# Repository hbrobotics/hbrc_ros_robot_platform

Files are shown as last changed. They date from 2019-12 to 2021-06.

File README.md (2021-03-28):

<!--
MIT License

Copyright 2020 Home Brew Robotics Club

Permission is hereby granted, free of charge, to any person obtaining a copy of this
software and associated documentation files (the "Software"), to deal in the Software
without restriction, including without limitation the rights to use, copy, modify,
merge, publish, distribute, sublicense, and/or sell copies of the Software, and to
permit persons to whom the Software is furnished to do so, subject to the following
conditions:

The above copyright notice and this permission notice shall be included in all copies
or substantial portions of the Software.

THE SOFTWARE IS PROVIDED "AS IS", WITHOUT WARRANTY OF ANY KIND, EXPRESS OR IMPLIED,
INCLUDING BUT NOT LIMITED TO THE WARRANTIES OF MERCHANTABILITY, FITNESS FOR A PARTICULAR
PURPOSE AND NONINFRINGEMENT. IN NO EVENT SHALL THE AUTHORS OR COPYRIGHT HOLDERS BE LIABLE
FOR ANY CLAIM, DAMAGES OR OTHER LIABILITY, WHETHER IN AN ACTION OF CONTRACT, TORT OR
OTHERWISE, ARISING FROM, OUT OF OR IN CONNECTION WITH THE SOFTWARE OR THE USE OR OTHER
DEALINGS IN THE SOFTWARE.
-->

# HBRC ROS Robot Platform

The HBRC ROS Robot platform (ie. HR<Sup>2</Sup> or just plain HR2) is a
pedagogical robotic platform for teaching various robotics skills.

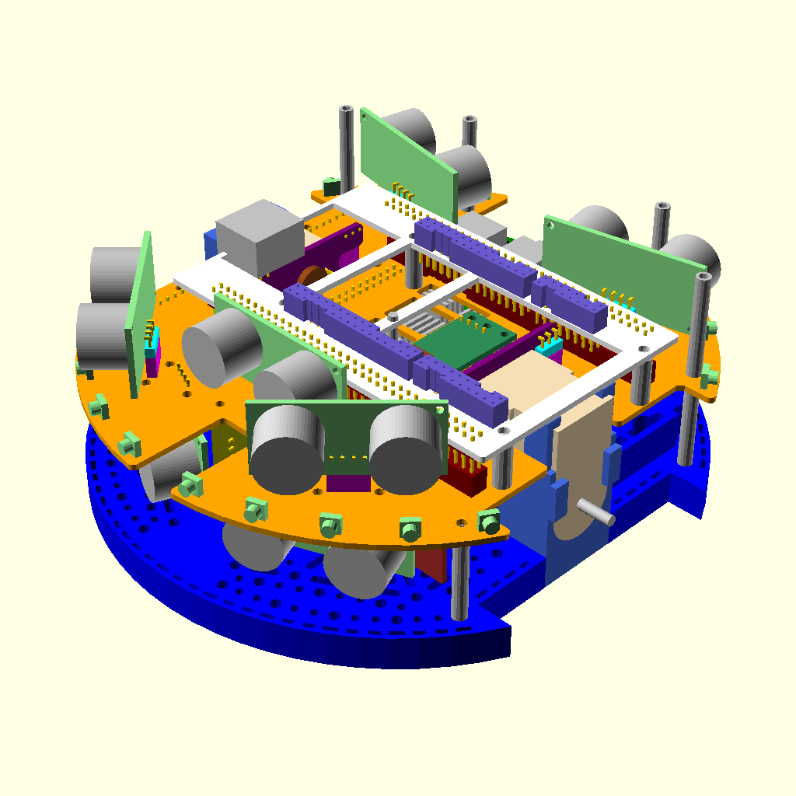
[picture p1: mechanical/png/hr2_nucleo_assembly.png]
HR2 Robot


This top level document is broken into the following sections below:

* [Google Group](#google-group):
  The Google Group mailing list for this project.

* [Goals/Requirements](#goalsrequirements):
  The goals and requirements for the project.

* [Mechanical](#mechanical):
  The mechanical engineering aspects of the project.

* [Electrical](#electrical):
  The electrical engineering aspects of the project.

* [Software](#software):
  The software engineering aspects of the project.

* [Education](#education):
  The education components of the project.

* [Download, Installation and Workflow](#download-installation-and-workflow):
  The download, installation, and workflow portions of the project.

* [Talks](#talks):
  Various talks given about the project.

## Google Group

There is a Google Groups mailing list to discuss this project at
[HbrcRosRobotPlatform@GoogleGroups.Com](mailto:HbrcRosRobotPlatform@GoogleGroups.Com).
To join the group, visit the
[HBRC ROS Robot Platform web page](https://groups.google.com/d/forum/hbrcrosrobotplatform)
(i.e. `https://groups.google.com/d/forum/hbrcrosrobotplatform`) and request to join.
If that does not work, squirt a quick message to the group manager
(`Wayne` AT_SIGN `Gramlich` PERIOD `Net`) requesting an invitation to join the group.

Not all traffic on the group is going to be interesting to everybody else.
To help out with filtering please put one of the following prefixes at the
front of the each subject line:

* `ALL:` A message of interest to everybody.
* `INST:` A message concerning software installation.
* `ME:` A message to people interested in the HR2 Mechanical Engineering 
  (i.e. solid modeling.)
* `EE:` A message to people interested in the HR2 Electrical Engineering
  (i.e. PCB design, manufacture, bring-up, testing, etc.)
* `SE:` A message to people interested in the HR2 Software Engineering
  (i.e. programs, firmware, etc.)
* `ED:` A message to people interested in the HR2 course materials.
* `DEV:` A message concerning downloading, installation, and development.
* `MSC:` A miscellaneous message that does not really fit any of the above
  protocols.

That should be enough group mailing list structure for starters.

## Goals/Requirements

The list below summarizes the some of the design choices that have been
made so far.

* Start with the Pololu Romi platform used by FPGA class. [Decided]
* Use Patrick's PCB breakout board as a starting point. [Done]
* Consider ditching the Pololu motor board. [Done]
* Work hard to see if the Pololu arm can be bolted on. [Very Likely]
* Try to use USB battery pack instead of AA batteries. [USB Pack yes; AA's no]
* Provide support RasPi 3B+ and RasP4: [yes]
  * 40-pin connector.
  * I2C EEPROM for "hat" identification.
  * Real Time Clock needed for ROS.
  * Various RasPi I2C, SPI, GPO, Serial lines made available.
    *  [Serial: yes, I2C: yes, SPI: probably not, GPIO: OS shutdown
* Some sort of MPU on board:
  * Off the shelf microcontroller board [STM Nucleo-144 Dev. Board format selected]
  * Roomy enough to run MicroPython/MicroROS [STM NUCLEO-F767ZI nominal]
    * ~$25, 216MHz, 2MB Flash, 512K RAM, timers, UARTs, I2C, SPI, Ethernet, etc.
  * Must support C/C++ debugging [ST-Link].
  * Ethernet Phy to talk to boards other than RasPi [Yes]
* FPGA support [custom daughter board required.]
* Arduino support [AVR Dropped. AVR's are expensive/under powered]
* Expansion Capabilities:
  * Arduino Shields. [One can be plugged onto Nucleo.]
  * MikroBus [Iffy, space is tight]
  * Demand Peripherals Connector(s): [On FPGA daughter boards only]
  * Wayne's Bus? [Iffy, space is tight; ouch this hurts!]
  * Grove connectors [Very Likely]
  * Pololu power supply sockets [Iffy, space is tight.]
* Sensors:
  * Motor encoders. [Yes, 1440 step/rev.]
  * Various edge sensors for table top challenge, maze follower, etc.
  * Edge sensors (TOF, IR)
  * Sonars, the are cheap [5 in front, 4 in back.]
  * Servos (arm, camera tilt) [Minimum 4 required]
  * Inexpensive Lidar [Only if the platform is not overloaded]
    * YLidar X2 (~$70)
    * RPLdar A1M8 (~$100)
  * E-Stop [Probably not]
* Camera [RasPi Camera]
* Misc:
  * What issues are missing?

### Mechanical

The mechanical issues are worked out in greater detail in the
[mechancial directory](mechanical/README.md).

The mechanical tasks are:

* Model the Romi platform in OpenSCAD to ensure that the PCB outline
  and mounting holes are correct.
* Model the Romi arm in OpenSCAD to make sure that the Arm does not
  interfere with anything.
* Model both a RasPi 3B+ and RasPi4 for attaching to PCB.
* Model the basic PCB outlines, connector placements, etc.

A short summary of the mechanical design decisions to date are:

* Use the Pololu Romi Platform.
* Use an alternate layout of the motor encoder PCB to free up space to
  support some SBC (Single Board Computers) that are larger than the
  Raspberry Pi footprint.
* Design master board to use an STM Nucleo-144 development board for the
  processor.  All H-bridges, power management, to be put on one board.
* FPGA boards to be done with a a daughter board that plugs into Nucleo-144 board.
 
## Electrical

The electrical issues are worked out in greater detail in the
[electrical directory](electrical/README.md).

Some brief comments on the electrical aspects are:

* The design is to be done using KiCad, since KiCad is 100% free.
* It would be nice to be able to use a simple two layer PCB.
* It would be nice to be able to take power from a USB Power pack.
* It would be nice to support daughter boards for FPGA's.

The overall strategy is to prototype everything using the
[Bantum Labs PCB Milling Machine](https://www.bantamtools.com/)
over at [OLogic](http://www.ologicinc.com/).  This machine is
constrained to only prototyping boards that are 4 inches by 5 inches.
Once the electronics are debugged and working, the PCB's will be
sent out to an appropriate PCB Manufacturing house.

### Software

This section is pretty brief for the moment...

The software issues are worked out in greater detail in the
[software directory](software/README.md).

Terminology:

* Single Board Computer (SBC):
  The nominal SBC for the platform is either the RasPi 3B+
  or the RasPi 4.  Other boards that are compatible with the RasPi
  pin-out *can* be supported, but somebody will have to step up to
  the task of doing the actual support.  The SBC resides on the robot.
* Micro-Processor Unit (MPU):
  This is the micro-controller that is on the main board.
  The nominal processor is ST32Fxxx, where xxx is to be decided.
  The MPU resides on the robot.
* Robot Processors: The robot processors are the SBC and the MPU.
* Development Processor: The development processor is not physically
  attached to the robot.  Instead, it communicates with the robot SBC
  via WiFi.

The software goals are:

* The platform runs ROS on the SBC.
  * Both ROS 1 and ROS 2 are goals with ROS 1 eventually being
    deprecated.
* We need to be able download firmware into the MPU from the SBC.
  This needs to be hands off.
  * Custom C/C++ drivers.
  * MicroPython.
  * Micro ROS.
* The development processor needs to be able to debug code
  running on the robot:
  * Debugging ROS nodes running on the SBC should be relatively easy.
  * Debugging C/C++ code running on the MPU is going to need JTAG
    support.  This can be done with a JTAG chip like the FTDI FT2232.
    This *may* be an "add-on".  OpenOCD can talk to this JTAG chip
    and `gdb` can talk to openocd.
  * Debugging MicroPython is tough.  It currently supports breakpoints
    but does not support data/stack inspection (yet!)
  * As a total stretch, it would be nice to support ARM ETM CoreSight.
    This requires a seriously expensive brick that weighs a ton.
    It is probably a fantasy.
* We need to support FPGA development:
  * We need to be able to download the FPGA chip from the SBC.
  * The FPGA compliation stack needs to run on the SBC and the development
    processor.

## Education

This section is more of a place holder for now...

A partial list of possible educational classes for HR2 platform are:

* Low level robot peripheral drivers.
  * C/C++
  * Micropython
* ROS driver development
  * C/C++
  * Python
* More generic ROS Programming
* Image processing with OpenCV
* AI Frameworks
* Arm manipulation
* PCB design
* MCAD design
  * OpenSCAD
  * Fusion 360
  * FreeCAD
* FPGA class
* Soldering Skills
  * Basic Through Hole
  * Surface Mount
* Rapid PCB prototyping w/Bantum Labs
* etc.

## Download, Installation, and Workflow

Software downloading and installation is done using the following basic steps.

1. [Optional Ubuntu Virtual Machine Installation](#optional-ubuntu-virtual-machine-installation]):
   For now, this project is developed exclusively using a Ubuntu 18.04LTS (Long
   Term Support) Linux distribution.  If you are not running Ubuntu 18.04LTS,
   you need to install it so that it runs using a virtual machine emulation software.
   Otherwise, this step can be skipped.

2. [Download and Install Software](#download-and-install-software):
   The HR2 project uses a diverse set of software.  This software is installed
   using some installation scripts followed by some tried and true technology
   called recursive Make.

3. [Workflow](#workflow):
   Modifications to the documention and design files is done using the
   [GitHub pull request workflow](https://guides.github.com/introduction/flow/).

### Optional Ubuntu Virtual Machine Installation

If you are running on either Windows or MacOS or a non-Ubuntu 18.04LTS Linux distribution,
you need to install Ubuntu 18.04LTS using virtual machine emulation software.  If you are
already running Ubuntu18.04LTS, you can skip this section right now.

There are many
(virtualization)[https://en.wikipedia.org/wiki/Comparison_of_platform_virtualization_software]
software products out there.  If you have a favorite, please feel free to use your favorite
virtualization product.  If you have no favorite, (VirtualBox)[https://www.virtualbox.org/]
is freely available and works.  The remaining instructions are in this section are for
VirtualBox.

Let's start off with some terminology:

* Host Machine:
  The host machine is the actual hardware and associated operating system that VirtualBox
  is running on.

* Guest Machine:
  The guest machine is the virtual hardware and associated operating system that is running
  under the VirtualBox software.  In this case, the guest machine is running Ubuntu18.04LTS.

The basic steps involved are:

1. Download VirtualBox:
   Visit the [VirtualBox Downloads] web page and follow the instructions appropriate
   for your host machine.

2. Download Ubuntu18.04LTS:
   [Download Ubuntu18.04 LTS](https://ubuntu.com/download/desktop) to your host machine.
   This shows up as a file with an `.iso` suffix.
   
3. Configure a VirtualBox Virtual Machine.
   Start VirtualBox software and a Graphical User Interface (GUI) should show up on your
   screen.

   Click on the [New...] button to bring up create pop-up window.

   A. Name and operating system:
      * Name: Pick a name, (suggestion: "Ubuntu18.04LTS").
      * Machine Folder: (Use the default.)
      * Type: Pick [Linux]
      * Version: Ubuntu (64-bit)
      * Click on [Next>].

   B. Memory size:
      * At least 4096 MB is recommended.  Do not use 1024 MB.
      * Click on [Next>]

   C. Hard disk:
      * Select "Create virtual hard disk now".
      * Click on [Create]

   D. Hard disk file type:
      * Select "VDI (VirtualBox Disk Image0"
      *Click on [Next>]

   E. Storage on physical hard disk:
      * Select "Dynamically allocated"
      *Click on [Next>]

   F. File Location:
      * Use the default file folder.
      * Increase the file size to at least 20 GB. 30 GB or 40 GB is preferred.
      * Click on [Create] to create the virtual machine and dismiss the pop-up window.

   G. Configure network:
      * Click on the [Settings...] Button to bring up [Settings] pop-up window:
      * Change "Attached to:" from "NAT" to "Bridged Adapter"
      * Click on [OK] to dismiss the pop-up window.

   The virtual machine is configured and ready to run.

4. Install Ubuntu18.04LTS.

   A. Start the virtual machine by either double clicking on the machine name or clicking
      on the [Start] button.  Please note that the guest machine and host machine can
      fight over who has the keyboard and mouse.  There are two control keys on your
      keyboard, one to the left of the space bar and the other to the right of the space bar.
      The right control key is used break up the fighting over mouse/keyboard input destination.
      If you are going "what happened to my mouse cursor are where are my keystrokes going"
      use the right control key to change things.

   B. After starting the virtual machine, VirtualBox will bring up a pop-up window
      asking you to select a virtual CD Rom image to to insert into the virtual optical
      disk drive.  Please use the file choose to select the Ubuntu 18.04LTS `.iso` file
      you previously downloaded.

   C. Click on [Install Ubuntu].

   D. Select your keyboard.

   E. Select: "Normal installation and download updates".

   F. Select: "Erase disk and install Ubuntu".
      * (Since this is virtual machine you can safely ignore the scary warning.)
      * Select Click on [Install Now]
      * Click on [Continue].

   G. Time Zone:
      *Select the correct time zone.

   H. Account setup:
      * Your name:
        Use your properly capitalize first and last name.
      * Your computer's name:
        Using a lower case name pick a name for the computer.
        For exam
      * Pick a user name:
        All lower case and one word.
      * Choose a password...:
        Type in your password twice.
      * Select "Require my password to log in".

   H. The installation takes some time.

   I. Click on [Restart Now]

   J. Ignore the "Please remove the installation medium" message, just press [Enter].

   K. Just type [Enter] for the Grub splash screen.

   L. Click on you user name and type in your password.

   M. Click through the startup screens.

   N. If the software updater window pops up click on [Install Now] and type in your password.
      If it pops up a restart machine window, just ignore it for now.

5. Install Guest Additions

   The guest extensions provide a more seamless integration between VirtualBox and
   the host machine.  For some reason, the documentation at for VirtualBox guest
   extension installation is actually pretty confusing.  Please try the instructions below:

   A. Bring up a terminal window by typing [Ctrl-Alt-T]  (use the left [Ctrl] key.)

   B. Type the following commands.  `sudo` will probably prompt you for your password.
   
      * `sudo apt update`
      * `sudo apt install build-essential dkms linux-headers-$(uname -r) --yes`

   C. Click on [Devices => Insert Guest Additions CD Image...]

   D. It should ask if it is OK to run some files.  Click [OK].

   E. Type in your password and click [Authenticate].
      This can take a while.

   F. Type [Enter] when [Press Return to close this window...] shows up.
      If your virtual machine reboots you can skip the next step.

   G. (Optional) If for some reason the virtual guest extensions do not properly
      install.  The following commands provide and alternative way of
      getting them installed.  Now run the following commands:

      * `sudo mkdir -p /tmp/cdrom`
      * `sudo mount /dev/cdrom /tmp/cdrom`
      * `sudo sh /tmp/cdrom/VBoxLinuxAdditions.run --nox11`
      * `sudo shutdown -r now`

      The machine should reboot.

   H. Select your user name and login with your password.

   I. Resize the virtual machine window to make sure the guest additions have taken hold.
      The background window should fill as it resizes.  If not, it will stay at a fixed
      size and something has gone wrong with your guest additions install.

   J. In the upper right corner there is a downward pointing triangle.
      Click on it and select [power off].
   
   Your virtual machine is installed and in a powered down state.

6. Make a clone.

   Installing all of the software is sufficiently painful that it is desirable
   to avoid having to do it again.  VirtualBox allows you to make a clone of
   an existing system so that the original system can be reused in the future.
   It is really easy and does not consume very much extra disk space,
   so making a clone is strongly recommended.

   A. Bring up the VirtualBox manager window again.

   B. Right mouse click on the name of your virtual machine:

      * Name: Give the clone a new name like "Ubuntu18.04LTS_HR2"
      * Path: Use the default
      * MAC Address Policy: Use the default
      * Leave the additional options unclicked.
      * Click [Next>] to go to the next pop-up window.

   C. Clone type

      * Select [Linked clone].  This saves lot's of disk space
      * Click on [Clone] to finish the clone.

   D. Now start the clone by by double clicking on it.

## Download and Install Software

The software is generally deployed in three broad catagories:

* Ubuntu packages: for basic tools and software (e.g. Kicad, OpenSCAD, etc.)
* Cloned Git Repositories: this project and some projects it depends upon used
  `git` repositories.
* Python `pip` packages: There is lots of Python 3 code sprinkled around this project
  and a bunch of it is packaged up as Python packages that can be installed with
  the Python `pip` program.  (By the way, `pip` stands for `Pip Installs Packages`.)
  There is heavy use of a technology called Python Virtual Environments.

There will be a number of cloned git repositories and they need to reside as
separate sub-directories under one parent repository directory.  (One parent
directory to rule them all!)  You can call this parent directory whatever you
want -- `repos`, `projects`, `funstuff`, `sauron`, etc.  For the directions
below we use `REPOS` for this parent directory name.  Please substitute the
directory name you picked for `REPOS` in the directions below:

### Clone 

There are 3 broad steps:

1. The first step is to clone the `hbrc_ros_robot_platform` repository.
   Let's get going:

        cd .../REPOS   # Change the current working directory to REPOS
        # We need to get `git` installed.
        # If `git` is already installed, skip the install below:
        sudo apt install git --yes # You may be asked for your user password:
        # Now "clone" the `hbrc_ros_robot_platform` repository using `git`:
	git clone https://github.com/hbrobotics/hbrc_ros_robot_platform.git
        # Change the current working directory to the root of the cloned repository
        cd hbrc_ros_robot_platform
	# Set your `git` user name and `email`.  Please run the following two commands:
        git config --global user.name "Your Name"
        git config --global user.email "youremail@yourdomain.com"

2. The second step is to run one `hr2_install` script.  This is done by

     ./bin/hr2_install OPTION

   where `OPTION` is one or more of the following:
   * `all`:  Installs everything.
   * `most`: Installs everything but `dev`.
   * `dev`:  Installs the development workflow (a personal Git.Hub account is required.)
   * `ee`:   Installs all of the software needed for electrical engineering.
   * `me`:   Installs all of the software needed for mechanical engineering.
   * `sw`:   Installs all of the software needed for software development.

   Many people select the `most` option.

   Downloading everything takes quite a while (frequently in excess of half an hour.)
   Sometime you will be prompted for your user password so that the system can install
   some system software.  The `stm32cubeide` software download (selected by `ee`, `me`)
   is particularly slow.
     
3. After the `hr2_install` script terminates (
   This is important.  You need to activate your Python Virtual environment.
   This is done as follows:

     source ~/.bashrc
     workon hr2   # Activate the hr2 Python virtual environment

4. After that yo can use the `make` program to do any remaining buidling.

   Use the `make` program to recursively build `everything` by typing:

           make everything

Installing is a notoriously fragile process and it is quite possible that
something can go wrong.  If so, please send a message to the group list with
the `DEV:` prefix on the subject line explaining the issue so it can be resolved.

### Workflow

Workflow is a generic term for how modifications are made to this project.

Examples of such modifications are.

* Modifying the mechanical models,
* Modifying electrical design and associated printed circuit board designs,
* Modifying the software,
* Fixing documentation errors,
* Developing educational course materials, Etc.

Some terminology here.  We are going to use the pronoun "you" to mean "you the
person doing project development" in the description below.

#### Workflow Introduction

There are two common workflows supported by GitHub.com:

* Shared Repository Workflow:
  This is the simplest model where there is one common shared parent repository stored
  at GitHub.com and you have local cloned copy of the shared parent repository stored
  locally on your development machine.  You develop and test your changes on your local
  machine.  When you decide your changes are "ready", you "push" the changes back up to
  the shared parent repository on GitHub.com.  Over time, you and other developers
  "pull" the accumulated changes stored in the parent repository down into your
  respective local repositories to stay up to date.  This workflow is extremely
  common and has been supported by many version control systems for literally decades.

* Fork and Pull Request Workflow:
  In this model, the common parent repository is the same as the shared repository
  workflow immediately above.  However, now you need two repositories to do development.
  The first repository is the same local repository on your local machine as before.
  In addition to your local repository, you also have your own semi-private
  repository stored on GitHub.com that is used for staging purposes.  This staging repository
  is goes by a less descriptive name called a "fork repository".  Your fork repository
  is "connected" to the shared parent repository.  Since there are multiple developers,
  there multiple "forks" of the same shared parent directory on GitHub.com, where each
  is stored in a different user account to keep them separate from one another.

  The workflow is that you make modifications to your local repository and "push"
  them up to your staging "fork" repository.  Next, you generate something called
  a "pull request".  (Frankly, the term "pull request" is miss-named, it should be
  called a "merge request".  It is too late to change the terminology now, so we
  will stick with the less descriptive term of "pull request".)  The details of how
  to generate a "pull request" are discussed  little be further below.  The "pull request"
  generates an E-mail that is sent to one or more reviewers.   The reviewer looks at your
  changes using the GitHub.com GUI (Graphical User Interface.)  If the reviewer likes
  the changes, they are immediately accepted and merged from your fork repository to
  the shared master repository.  If any reviewer has some issues, an E-mail dialog ensure
  where the reviewer says things like "I really like this!", "This won't work because ...",
  "Fix this tiny issue", "What about doing it this way...", and an occasional
  "No way because..."  As a result of some of the review comments, you may need to make
  additional changes and push them up to the fork repository.  When the pull-request
  E-mail exchange dialog dies down and all of your changes have been pushed up to your
  fork repository, the reviewer accepts the changes and merges them into the
  shared parent repository.  The "Fork and Pull Request Workflow" is shown immediately
  below using some crude ASCII art:

                [Shared Parent]<---------------[Simi-Private Fork]   GitHub.Com
                       |                                ^
                ====== | ============================== | =====================
                       v                                |
                       +--------->[Private Local]------>+         Local Machine
                        
                         Fork and Pull Request Workflow
			   
The key advantage of the Fork and Pull Request work flow is that you do not need
permission from anybody to start making your changes.  You start your changes locally
and ask for permission only after you think they are ready.  When the reviewer
agrees, your changes are merged in.

It should come as no surprise to you that this project is using the fork and pull
request workflow.

#### Workflow Setup

If you have followed the download and install instructions above, you have a
local copy of the `hbrc_ros_robot_platform` repository as a sub directory under
your REPOS directory.  What you do not have is a staging fork repository *AND*
you have not configured `git` to do an asymmetric pull and push.  The instructions
below will remedy these issues.

Most of the tools you need to do the Fork and Pull Request workflow are already mostly
in place.  The primary tools are `git` and a program called `hub` which is a command
line interface to the GitHub.Com functionality.  We will do as much of the set up using
a command line tools as possible because the command line tools tend not to change as
fast as the web interface changes.  (If you are already comfortable the GitHub.Com web
interface, you can probably skip some of the steps below and use the web interface instead.)

There are a still a few manual steps to do:

1. The first step is to create your own personal account on GitHub.Com.  This is done
   visiting the main [GitHub.Com web page](https://github.com/) web page.  You need to
   specify a unique "Username" (all lower case with no spaces or punctuation is recommended),
   an "Email" address, and a "Password".  There will be a message sent your E-mail address
   that you must respond to with a response E-mail to finish the account creation.  The
   "Username" is your GitHub.Com account name and will be needed further below.  Do not
   log out of GitHub.Com yet.

2. In order to avoid having to type in a password all the time, you need to set up your
   computer to use an SSH key to talk to your GitHub.Com account.  The install scripts
   have ensured that an SSH key has been generated.  The public key is stored at
   `~/.ssh/id_rsa.pub`.  There is a
   [GitHub.Com SSH Key Installation](https://help.github.com/en/github/authenticating-to-github/adding-a-new-ssh-key-to-your-github-account) web page that will guide you through the GitHub.Com
   web interface to install your public SSH key.  It is a little tedium for now, but will avoid
   much password prompting annoyance in the future.  If you are lucky, you should not need
   to deal with the GitHub.Com web interface any more.  Now you can disconnect from GitHub.Com.

3. Add GITHUB_ACCOUNT_NAME variable definition to your `~/.bashrc` file.  This is typically
   done a the end of the file by adding a line that looks like:

      GITHUB_ACCOUNT_NAME=whatever_you_typed_in_in_the_previous_step
      source ~/.bashrc  # Do no forget this step.

4. Please rerun the `hr_install dev` to get your development environment set uo.

That pretty much wraps up the additional steps need to enable the "Fork and pull-request"
workflow.  Next, it is time to try it out.

#### Workflow Usage

The `git` program does a great deal of stuff and it is outside the scope of this
document to attempt to cover it all.  Instead, we will explain just enough to get started.

If you have followed the steps above, you have a repository named `hbrc_ros_robot_platform`
sitting on you local machine.  Your local repository has the following characteristicx:

* It has `upstream` remote descriptor that points to the shared project repository.
* It has `staging` remote descriptor that points to the semi-private forked directory
  that is used for staging purposes.
* The `master` branch which has be set up so that it only accepts updates from the
  `upstream` remote.

The first thing to understand is that you should never to development on the `master`
branch.  We have tried to make it difficult for you to screw up `master`, but somebody
who really wants to can screw it up anyhow.

The second thing to understand is that all development takes place in one or more
side branches, called development branches.  The way to create a new branch is by

     git checkout -b NEW_BRANCH_NAME master

where you supply a new and hopefully descriptive name for the new development branch.
After this command, the new branch will be active.  Now you can modify things to your
hearts content.  You can check the files in as many times as you want using `git add ...`
and `git commit -m "SOME MESSAGE HERE."`.  You can perform as many commits as you want
on the branch.  Please put descriptive comments in the commit logs.

When you think you changes are ready to be merged into the project you initiate
a pull-request.  This is done by the command:

     pull_request

This command is in the repository `bin` directory.  This will ensure that you have
merged with the `master` branch, push your commit up to the staging repository and
generate a pull request.  You will have add a comment into the pull request via an
editor that will pop up.

Just so you know, there is a command called `master_merge` that will ensure that
the `master` branch is up to date with GitHub.Com and then attempt to `master` branch
to be merged with your current branch.  This command is invoked by `pull_request`, but
you can invoke it yourself if you just want to merge without triggering a pull request.

That is basically it.

The current files in the `bin` directory are:

* `hr2_install`:
  An installation script for install HR2 project software.

* `master_merge`:
  A script that ensures that the `master` branch is up to date and then attempts
  to merge the `master` branch into your branch.

* `pull_request`:
  A script the forces a `master_merge` followed by generating a pull request for GitHub.Com.

* `stm32cubeide`:
  A symbolic link to a `stm32cubeide` program.  This is basically the Eclipse programming
  environment that has been configured to work with the `stm32cube` software for supporting
  STM32 micro-controllers.

* `xstm32cubeid`:
  This is a shell script that attempt to attach to an externel (i.e. remote) ST-Link
  before starting the stm32cube.
  This is preformed using an the `usbip` (i.e. USB Internet Protocol) for remote access to USB devices.

More scripts are likely to be added over time.

#### Coding Style

The vast majority of the code is written in Python, C, and some Shell scripts.

* Python:
  Python 3 only.  All of the code is pushed through `mypy` (with type-hinting),
  `flake8` to catch coding issues, and `pydocstyle` to catch documentation issues.
  In general, the pretty standard coding style for Python is used.  One quirk is that
  Wayne Gramlich hates the `self` variable and usually assigns it to a more descriptive
  variable name.  Other than that, it is pretty standard.

* C:
  Pretty standard C coding style is used.  There are 4 spaces for each indentation level.
  The "then" clause of an if statement always has {...}, no exceptions.

* Shell:
  Shell scripts are tedious to write and debug and still tend to be fragile.
  Lot's of comments are used.  The `set -xeuo pipeline` command is used for debugging
  when possible.

All documentation is written in [markdown](https://daringfireball.net/projects/markdown/).
Speaking of documentation, it is treated just like code in that it has bugs in it as well
(miss-spelled words, bad grammar, unclear desciptions, etc.)  The documentation is fixed
the same way that code is fixed, using the standard workflow.

Eventually we will use the Github issue tracker to track both code and documentation issues.
For now, the group mailing list will be used instead.

## Talks

Occasionally, talks are give about this project and the talk materials are organized into the 
[talks](talks/README.md) directory.

<!-- Random

        ;;; Make emacs notice when buffers change due to switching branches:
        (global-auto-revert-mode 1)

#### Stm32CubeIDE

* Downloand `en.st-stm32cubeide_1.3.0_5720_20200220_1053_amd64.deb_bundle.sh.zip`from STM website.
* `mkdir /tmp/cube`
* `unzip -d /tmp/cube en.st-stm32cubeide_1.3.0_5720_20200220_1053_amd64.deb_bundle.sh.zip`
* Unpacks into `st-stm32cubeide_1.3.0_5720_20200220_1053_amd64.deb_bundle.sh`
* Set execute bit `chmod +x st-stm32cubeide_1.3.0_5720_20200220_1053_amd64.deb_bundle.sh`
* Execute `/tmp/cube/st-stm32cubeide_1.3.0_5720_20200220_1053_amd64.deb_bundle.sh`
  * It prompts for sudo password.  Not clear what it does under sudo.
* Unpacks a bunch of stuff into the `/opt/st/stme2cubeide_1.3.0_stm32` directory.
* Execute `/opt/st/stm32cubeide_1.3.0_stm32/stm32cube`

#### Removing big binary blobs:

We are trying to delete: `stm32cube_download/stm32cube.tar.bz2.0{0,1,2,3,4,5,6,7,8}` from
the repository.  It looks like `bfg` is the recommended program for doing the deletion.
Make sure that the files have been `git delete`'ed and pushd up to GitHub.Com.
Rename the current repo from `kicube32` to `kicbube32_delete_me`.  Hopefully we will
not be using the repo any longer...

Some URL'S:

* [BFG](https://rtyley.github.io/bfg-repo-cleaner/)
* [BFG Example](https://github.com/IBM/BluePic/wiki/Using-BFG-Repo-Cleaner-tool-to-remove-sensitive-files-from-your-git-repo)
* [Another BFG Example](https://medium.com/@prankulgarg/want-to-remove-large-files-blobs-from-git-history-permanently-4723e72a84e1)

     # Download the repository to be modified:
     cd /tmp
     time git clone --mirror git@github.com:waynegramlich/kicube32.git
     # Generates a file called `/tmp/kicube32.git`.

     # Make a backup:
     time tar xvf /tmp/kicube32.git.tar kicube32.git.tar

     # Download `bfg`:
     # `wget https://repo1.maven.org/maven2/com/madgag/bfg/1.13.0/bfg-1.13.0.jar -O /tmp/bfg.jar`

     # Make sure we have java installed:
     which java

     # Run `bfg`:
     time java -jar bfg.jar --delete-files stm32cube.tar.bz2.0{0,1,2,3,4,5,6,7,8} /tmp/kicube32.git

     # Do final cleaunp:
     cd /tmp/kicube32.git
     time git reflog expire --expire=now --all && git gc --prune=now --aggressive

     # See how you did:
     du -sh *

     # Add a remeote back in:
     git remote add upstream git@github.com:waynegramlich/kicube32.git
     git push --force upstream master

    * https://stackoverflow.com/questions/6335717/can-git-tell-me-if-a-merge-will-conflict-without-actually-merging

        git merge --no-commit branch2
        # check the return code here
        git merge --abort

;;; Make emacs notice when buffers change due to switching branches:
(global-auto-revert-mode 1)

-->

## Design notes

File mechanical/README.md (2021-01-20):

<!--
MIT License

Copyright 2020 Home Brew Robotics Club

Permission is hereby granted, free of charge, to any person obtaining a copy of this
software and associated documentation files (the "Software"), to deal in the Software
without restriction, including without limitation the rights to use, copy, modify,
merge, publish, distribute, sublicense, and/or sell copies of the Software, and to
permit persons to whom the Software is furnished to do so, subject to the following
conditions:

The above copyright notice and this permission notice shall be included in all copies
or substantial portions of the Software.

THE SOFTWARE IS PROVIDED "AS IS", WITHOUT WARRANTY OF ANY KIND, EXPRESS OR IMPLIED,
INCLUDING BUT NOT LIMITED TO THE WARRANTIES OF MERCHANTABILITY, FITNESS FOR A PARTICULAR
PURPOSE AND NONINFRINGEMENT. IN NO EVENT SHALL THE AUTHORS OR COPYRIGHT HOLDERS BE LIABLE
FOR ANY CLAIM, DAMAGES OR OTHER LIABILITY, WHETHER IN AN ACTION OF CONTRACT, TORT OR
OTHERWISE, ARISING FROM, OUT OF OR IN CONNECTION WITH THE SOFTWARE OR THE USE OR OTHER
DEALINGS IN THE SOFTWARE.
-->

# HBRC ROS Robot Mechanical Issues

The "nominal" base for the HR<Sup>2</Sup> is the
[Pololu Romi Chasis](https://www.pololu.com/category/202/romi-chassis-and-accessories).
However, other bases can be considered.

## Software Installation

Do the following:

     cd .../hbrc_ros_robot_platform/mechanical  # Move to the `mechanical` directory.
     ./install_me.sh  # Run the reentrant installation script; prompts for root password
     workon hr2  # Enable the `hr2` python virtual environment.

To build everything and view it:

     make
     openscad hr2_models.scad -D 'name="hr2_arm_assembly"'

## Mechanical Requirements:

The section below is a wish list of mechanical "requirements" for the HR2.
Not all of these requirements are expected to be met.

### Base Requirements

The base requirements are:

* Use a COTS (Commercial Off The Shelf) platform.
* Differential Drive with a relatively large wheel diameter.
  * A maximum forward speed of 30cm/sec.  10 cm/sec. is acceptable.
* Over 1000 ticks per revolution odometry.
* Front and rear ball castors with low rolling friction.
  * One of the ball castors must be "floating" to deal with uneven floors.
* Runs off of rechargeable batteries.  A USB battery pack would be ideal.
  * The mass of the batteries must be along the robot center-line to
    prevent the robot from veering to one side.
  * The mass of the batteries must be towards the rear non-floating ball
    castor.
  * It would be nice if the battery pack could be easily swapped out.

### Sensor Requirements

The sensor goals are:

* Bottom reflectance sensors for edge detection and/or line detection.
  Pololu QTR/QTRX/QTRLX sensors are acceptable.
* Time of flight edge sensors.  SparcFun SEN-12787 will work.
* Sonars: SR04's sensors from China are inexpensive (and not of the
  highest quality).  5 Sonars in front and back with 22.5 degree angular spacing
  and 4 in the rear.  The sonars can be alternated to mounted on top and on bottom
  of the same PCB to save space.  There is an mechanical interference issue with
  the forward sonar and the arm.
* Bump Sensor: An inexpensive front and rear bump sensor is desired.
  It can be extremely simple.
* E-Stop Button: It is nice to have an E-stop button that is readily
  available, when the robot code goes bad.  The E-stop would disable
  the motor drivers.
* Lidar: An optional inexpensive 360 degree Lidar is very desirable.
  ComputerShop sells a bunch -- YLIDAR X4 ($99), YLIDAR G2 ($159),
  YLIDAR X2 ($69), RPLidar A1Mi ($99).
* Cameras:
  * It would be nice to have an optional forward facing camera
    for object detection, etc.
  * It would be nice to have an optional upward facing camera
    for fiducial navigation.
  * It may be possible use one camera and a servo to be able to
    do both.
* Microphone: It would be nice to be able to talk to the robot.
  * A directional microphone would be cool so that the robot can
    turn towards a speaker.
* Speaker: It would be nice if the robot could talk back.

### Actuator Requirements:
	
The actuator goals are:

* Gripper Arm: An optional arm with gripper is desirable:
  * The Pololu Romi Arm is acceptable.  It is not required to mount it
    on the Pololu expansion plate; it can be mounted forward.  Managing
    center of mass is important.
  * Non-Gripper Arms: It would be fun if there is a "arm" on each side so
    that the robot can wave its "arms".  There are no grippers on these
    side arms.  This goal is not looking too good right now.

### Indicator Requirements:

The indicator requirements are:

* LED's:
  * Front LEDS:
    * For debugging and fun there needs to be a line of LED's
      in the front.  Being able to do a Knight Rider LED sweep would be fun.
  * Rear LEDS:
    * It would be nice to have both Rear LED's that can glow read for
      braking and white for reverse (i.e. back up lights.)
* LCD: An optional LCD would be nice.
  * Ideally, this can be connected to the SBC as an output device.
  * If placed immediately below the 3D camera it can be programmed
    to be a mouth that can smile,  frown, smirk, etc.
  * If a standard size is selected, it can play video clips. (Woo Hoo!)
    
### Miscellaneous Requirements:	

The miscellaneous requirements are:

* Miscellaneous:
  * Docking Station:
    * An optional docking station would be nice.  It can be *VERY* simple.
  * USB devices:
    * Keyboard/Mouse: For debugging, a keyboard and mouse is desirable.
      * Wireless keyboard and mouse is OK.
    * Game Controller:
      * Wireless remote controller is used to drive the robot around.
  * Carrying Handle: It would be very nice to be able to pick up the
    robot with a handle.
  * Carrying Case: Strictly optional, but being able to cart the robot
    around in some sort of clear case would be nice.
  * Mount points:
    * It would be nice to provide some mount points for other expansions
      modules like Seeedstudio Grove.  This is basically a 10mm x 10mm
      grid of holes.  These can be both internal and/or external.  There
      needs to be cable access holes for externally mounted modules.

### Robot Skin requirements:

The robot skin requirements are:

* A skin is optional, but very desirable.
* Humans like anthropomorphic robots because they are more "fun".
* Having a clear skin so people can see inside is very desirable.
  * Being able to print a paper skin would be neath.

### Non-requirements:

The explicit non-requirements are:

* This platform is not expected to be operated over uneven floors.
  Even going over door strips is *NOT* required.g

## Decisions Made so far:

The current (tentative) design decisions are:

* It looks like it is possible to support multiple different SBC's (Single Board Computers)
  as long as they are basically compatible with the Raspberry Pi mounting holes and 2x20
  male connector (i.e. RPi B+, 3A+, 3B+, and 4B.)  It is possible to take a Raspberry Pi
  compatible board that is quite a bit larger than the typical Raspberry Pie and make it
  fit.  The key to accomplishing this task was to abandon the standard Pololu shaft encoder
  PCB's in favor of one that is wider along the Y axis, but shorter in the Z axis.  Given
  how trivial the encoder PCB is, this is a workable solution. This allows one edge of the
  RPi compatible SBC to extend underneath one of the drive motors.

* The ST Microelectronics Nucleo-144 development boards have been selected as the basic
  microcontroller of the robot.  These are extremely popular development boards that STM
  tends to keep in stock across multiple vendors.  A few weeks ago, the entry level board
  was at about $15, but there seems to be a run going on so the prices have crept up.
  The reasons for selection this board are:
  
  * STM got beat up over and over again about moving peripherals around on their chips.
    Eventually they figured out that they had to keep all of the peripherals mapped
    to the same pins.  This does not mean that all chips support all peripherals, but
    instead if the peripheral is present on a chip, it is available exactly the same pins
    as every other pin on other boards that has the same peripheral.  As a result of
    this design decision, all of the Nucleo144 products use the exact same PCB with
    the only difference being the CPU chip and a label that specifies which CPU chip
    is mounted.  That's it.  One nice feature of this strategy is that as newer chips
    are released, they just ship a new Nucleo144 board with the new chip.  The new board
    should be pin-for-pin compatible with the older boards.  Hopefully, the Nucelo-144
    will be "future proof".

  * The larger Nucleo-144 boards like the STM32F676ZI has 2MB of flash memory that
    should be more that adequate for running MicroPython and Micro ROS.

  * The Nucleo-144 boards come with a small attached ST-Link debugger for software
    development.  For space reasons, this board has to be cut off and remounted
    elsewhere on the master board.  This *should* support software development
    using popular IDE's (Integrated Development Environments) such as vscode and
    Eclipse in conjunction with OpenOCD.

  * The Nucleo-144 boards come with an RJ-45 connector for connecting Ethernet
    to the SBC to allow high speed communication between the two devices.

  * The Arduino IDE with the boards manager *may* allow development on the smaller
    Nucleo-144 board such as Nucleo144-F476RG.  Presumably other larger boards can
    be added as needed.

* FPGA Strategy.  The current strategy is that any FPGA's will be adapted to the
  robot through the NUCLEO-144 ZIO connectors.

## Viewing the Models:

* Run `show_scad` to see variouls models.
  If no argument is specified, the list of available names to show is listed.

## Documentation:

### Remote Documentation

  * [Pololu Romi Chasis User's Guide](https://www.pololu.com/docs/0J68/all):
    The Pololu Romi is mostly documented by the Pololu web site.  Alas, there
    is no `.pdf` version of the file, so if Pololu ever decides to take the
    User's Guide down, it will be *GONE*.

### PNG Files
  
The `mechanical/png` directory is where various `.png` image files are stored.

The robot is assembled in the following order:

  1. [`mechancal/png/hr2_base_assembly.png`](png/hr2_base_assembly.png):
     Start with the Romi Chassis base, add *empty* motor holders and spacers
     to mount the "Pi" board and Master board on:
     <Br>
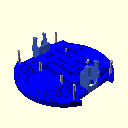
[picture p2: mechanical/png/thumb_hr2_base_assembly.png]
     

  2. [`mechancal/png/hr2_pi_assembly.png`](png/hr2_pi_assembly.png):
     Mount the Raspberry Pi compatible SBC (Single Board Computer)
     on the 4 spacers.  Since robots vibrate, it is recommended that every
     screw have a lock washer.
     <Br>
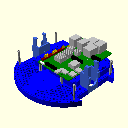
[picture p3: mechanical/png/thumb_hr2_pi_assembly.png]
     

  3. [`mechancal/png/hr2_master_assembly.png`](png/hr2_master_assembly.png):
     First mount the appropriate spacers on a master board (please use lock washers.)
     Also, there is a vertical alignment screw that needs to stick straight up.
     It is M2.5 and needs to be attached with a lock washer and a hex nut.
     Do not forget this screw, because it is really easy to plug the Nucleo144
     board in offset by one or more pins otherwise.  Improperly installing the
     the Nucleo144 can destroy it.  Next mount the master board onto the robot.
     The connector on the bottom of the board will plug into the 2x20 connector
     on the Pi compatible SBC.  Finally, screw in the screws that mount the master
     board to the appropriate spacers (use lock washers!)  Note: the female receptacles
     are frequently shown in "debug" mode so that notches of material are taken out the
     the sides so that it is possible to see how deep the mating male pins go into
     the receptacle.
     <Br>
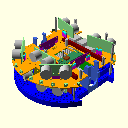
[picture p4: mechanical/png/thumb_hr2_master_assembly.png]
     

  4. [`mechancal/png/hr2_wheel_assembly.png`](png/hr2_wheel_assembly.png):
     Now assemble the two motor/encoder/magnet/wheel sub-assemblies.  The motor
     sub-assemblies are interchangeable; there is no left vs. right.  They
     are held in place by the plastic motor holder clips.
     <Br>
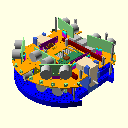
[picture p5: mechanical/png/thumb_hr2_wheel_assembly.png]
     

  5. [`mechancal/png/hr2_nucleo_assembly.png`](png/hr2_nucleo_assembly.png):
     Next, make sure that the veritcal alignment screw is still mounted
     sicking up.  If you did not install it back in step 3, go back to
     step 3 and install it.  It is really trivial to incorrectly install and
     destroy the Nucleo144 without the alignment screw.  Mount the Nucleo144
     onto the master board and screw it onto the 4 spacers (with lock washers.)
     Note that the Nucleo144 is frequently shown in debug mode with the center
     cut away to improve visiblity down to the mater board.
     <Br>
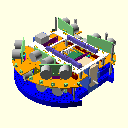
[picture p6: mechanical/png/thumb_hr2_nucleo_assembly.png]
     
  
That is it for now.

### DXF Files

  There are two generated `.dxf` files available:

  * [mechanical/dxf/expansion.dxf](dxf/expansion.dxf):
    The generated `.dxf` file from the OpenSCAD model
    for the Romi Expansion Chassis.

  * [mechanical/dxf/romi_base.dxf](dxf/romi_base.dxf):
    The generated `.dxf` file from the OpenSCAD model
    for the Rom Chassis Base.

  In addition, there is are two `.dxf` files supplied by Pololu
  that are archived in the `mechanical/dxf` directory.  These
  are copyrighted by Pololu and if Pololu objects to these being
  cached in this repository, they will be removed immediately
  upon a request from Pololu:

  * [mechanical/dxf/romi_chassis.dxf](dxf/romi_chassis.dxf):
    The `.dxf` that can be used to extract the various hole,
    slot and rectangles on the Romi chassis.

  * [mechanical/dxf/romi-chassis-expansion-plate.dxf](dxf/romi-chassis-expansion-plate.dxf):
    The `.dxf` that can be used to extract the various hole,
    slot and rectangles on the Romi expansition plate.
    
### PDF Files

  There are two cached `.pdf` files from Pololu.  Again these
  are copyrighted by Pololua nd if Pololu objects to these being
  cached in this repository, they will be removed immediately
  upon a request from Pololu:

  * [mechanical/pdf/romi-chasis-expansion-plate-dimensions.pdf](pdf/romi-chasis-expansion-plate-dimensions.pdf):
    The `.pdf` that contains many (but by no means all) of then
    dimensions of the Romi Chasis Expansion Plate.

  * [mechanical/pdf/romi-chasis-expansion-plate-hole_alignment.pdf](pdf/romi-chasis-expansion-plate-hole_alignment.pdf):
    The `.pdf` that contains information about which holes line up
    between the expansion plate the the main chasis plate.

## Models:

The models are store in some Python files, which upon execution generate
the associated OpenSCAD files.  There are two directories:

### `scad_models`

The `scad_models` directory currently contains:

* `scad.py`: This is a library of Python code that is used to generate
  an OpenSCAD `.scad` file.

* `hr2_models.py`: This is the Python code that builds all of the
  OpensCAD models using the `scad.py` liberary.

* `__init__.py`: This is the file that is required by Pythong to indicated
  that the `scad_models` directory contains a Python package.

The program `pydoc NAME.py` will print out the Python doc strings for some
Documentation.

### `tests`

The `tests` directory currently contains the Python Unit tests:

* `test_scad.py`: The unit tests for the `scad.py` library.

* `test_hr2_models.py`: A unit tests for the `scad_models.py` code.

## Miscellaneious:

There a a bunch of miscellaneous files in the `mechanical` directory:

* `README.md`: This documetation file.

* `setup.py`: This file is required by Python to construct the `scad_models`
  package.

* `develop.rec`: This is a list of Python packages that are used by this project.

* `Makefile`: There is a `Makefile` that is used to build everthing.
  It has the following three targets:

* `clean`: Removes all derived files to force a clean build.

* `all`: Build everything.  This involves:

  * Running the Python files through `mypy`, `flake8`, and `pydocstyle`.
  * Installing the `scad_modules` package in the Python virtual environment.
  * Runs the `hr2_models.py` program from the Python virtual environment to
    generate `hr2_models.scad`.
  * Generates various `.dxf` and `.png` files.

* `test`: Runs the Python unit test suites and outputs any code lines
   that is not covered by the test suites.

* [romi_base.csv](romi_base.csv): This is a `.csv` (Comma Separated Value) file that
  can be read in as a spreadsheet.  It identifies pretty much all of
  the holes, slot, and rectangles on the Romi Chasis with the origin
  set to the exact middle of the chassis.

* [romi_base.html](romi_base.html): This contains the same content as the `romi_base.csv`
  file, but in HTML table format.  It is easier to read in a web browser.

<!-- https://github.com/CadQuery/cadquery -->

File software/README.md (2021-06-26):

<!--
MIT License

Copyright 2020-21 Home Brew Robotics Club

Permission is hereby granted, free of charge, to any person obtaining a copy of this
software and associated documentation files (the "Software"), to deal in the Software
without restriction, including without limitation the rights to use, copy, modify,
merge, publish, distribute, sublicense, and/or sell copies of the Software, and to
permit persons to whom the Software is furnished to do so, subject to the following
conditions:

The above copyright notice and this permission notice shall be included in all or
substantial portions of the Software.

THE SOFTWARE IS PROVIDED "AS IS", WITHOUT WARRANTY OF ANY KIND, EXPRESS OR IMPLIED,
INCLUDING BUT NOT LIMITED TO THE WARRANTIES OF MERCHANTABILITY, FITNESS FOR A PARTICULAR
PURPOSE AND NONINFRINGEMENT. IN NO EVENT SHALL THE AUTHORS OR COPYRIGHT HOLDERS BE LIABLE
FOR ANY CLAIM, DAMAGES OR OTHER LIABILITY, WHETHER IN AN ACTION OF CONTRACT, TORT OR
OTHERWISE, ARISING FROM, OUT OF OR IN CONNECTION WITH THE SOFTWARE OR THE USE OR OTHER
DEALINGS IN THE SOFTWARE.
-->

# HR2 Robot Software

<!-- ==================================== 100 Characters ======================================= -->

This document discusses how to download, install, and develop software for the HR2 platform.
This document is currently broken into the following sections:

* [Introduction](#introduction):
  The introduction to the whole software development process.

* [Software Download and Install](#software-download-and-install):
  How to download and install the needed software.

* [Firmware Development](#firmware-development):
  The workflow for developing microcontroller firmware.

## Introduction

For the HR2 there are three computers/microcontrollers of interest:

* Development Computer:
  The development computer is used for all software development.
  It is a 64-bit x86 architecture processor that runs the Ubuntu 20.04 Linux distribution
  (possibly in under an emulator.)
  The development computer runs both [ROS2](https://index.ros.org/doc/ros2/) and
  the microcontroller development software  (discussed shortly below.)
  The development computer needs to be able to access a local WiFi network
  in order to communicate with the HR2 robot computer.

* Robot Computer:
  The robot computer is either a 4GB or 8GB  Raspberry Pi 4
  and runs ROS2 under the Ubuntu 20.04  Linux distribution.
  (By the way, 4GB of memory is more than adequate for the Raspberry Pi 4.)
  The robot computer acts as the intermediary between the Development computer
  and the Robot Microcontroller (see immediately below.)
  The Robot Computer communicates with the development computer via the local Wifi network.

* Robot Microcontroller:
  The robot microcontroller is an STM (ST Microelectronics) 32-bit microcontroller
  that resides on the HR2 robot that handles lower level functions (motors, sensors, etc.)
  Currently, it is an STM32F767ZI, but that could change later on.
  All microcontroller firmware is written and debugged on the development computer
  using a cross platform firmware development environment.
  The developed firmware is downloaded to the microcontroller
  using either a physical cable or over WiFi, whichever is most convenient.

The ultimate goal is to be able to develop all software on the development computer and
download/execute/debug the developed software to the appropriate computer.

There is some [additional needed hardware](#additional-needed-hardware) to perform the software
and firmware download.

## Software Download and Install

Each computer/microcontroller needs is its own software development software.
Please use hardwired network connections for all initial software installs.
Setting up Wifi properly is a discussed much further below.

This is broken into the following sections:

1. [Additional Needed Hardware](#additional-needed-hardware):
   Some additional cables, micro-SD cards, etc. are needed
   during software download and installation.

2. [Development Computer Ubuntu 20.04 Install](#development-computer-ubuntu-2004-install):
   Get the Ubuntu 20.04 Linux distribution running on your development computer

3. [Development Computer ROS2 Install](#development-computer-ros2-install):
   Install ROS2 (Foxy) on your development computer.

4. [Development Computer STM32CubeIDE Install](#development-computer-stm32cubeide-install):
   Install the STM32CubeIDE microcontroller software on development computer.

5. [Development Computer Configuration](#development-computer-configuration)
   Some additional configuration for the development computer.

6. [Robot Computer Ubuntu Installation](#robot-computer-ubuntu-installation)

7. [Robot Computer ROS2 Installation](#robot-computer-ros2-installation)

### Additional Needed Hardware

In addition to the three computers above in the [introduction](#introduction),
you need some additional hardware.
All of the possible needed hardware is listed here,
but discussed in greater detail in various sections below.

In the United States For the more specialized electronics,
[Digi-Key](https://www.digikey.com/) is a common electronics distributor.
Many of the other items can be purchased from vendors such as Amazon, NewEgg, etc.
For Digi-Key, links into their website are provided,
so you do not have to figure out how to find things on their website.

The additional required hardware is needed:

* [4GB Raspberry Pi 4](https://www.digikey.com/en/products/detail/raspberry-pi/RASPBERRY-PI-4B-4GB/10258781):
  This is robot computer immediately above in the [introduction](#introducion).

* [Raspberry Pi 4 Heat Sinks](https://www.digikey.com/en/products/detail/seeed-technology-co-ltd/110991327/10451876)
  The Raspberry Pi 4 runs hot and needs heat sinks.
  The HR2 master printed circuit board (PCB)  has holes in the board to radiate heat from the heat sinks.
  They come in package of 4 -- 1 large for the processor, 1 medium for the memory, and
  2 smaller ones for the Ethernet controller and USB controller.
  *DO NOT* power up the Raspberry Pi 4 microcontroller without first attaching the heat sinks.

* [Nucelo-F767ZI](https://www.digikey.com/en/products/detail/stmicroelectronics/NUCLEO-F767ZI/6004740)
  This is the robot microcontroller the [introduction](#introduction).

* Micro-SD to USB Adapter:
  There are plenty of these available out there.
  Search for "USB A to micro SD adapter".

* Micro-SD card:
  32GB micro-SD cards are pretty affordable.
  Make sure it is `UHS-1`.
  SanDisk is a common vendor, but there are others.
  These cards are really small and easy to lose.
  So keep careful track of them.
  Also, it does not hurt to buy an extra just in case you lose one.

* [Battery Pack](https://www.amazon.com/gp/product/B08F7XM5GN/ref=ppx_yo_dt_b_asin_title_o07_s00):
  The Raspberry Pi4 is powered via a USB-C connector.
  Batteries packs come and go.
  The one that is currently recommend is the CONXWAN 26800mAh Power bank.
  What is nice about this one is that it has 3 3A output connectors (1 USB-C and 2 USB-A).
  In addition, it can be charged either via the USB-C or via a forth USB micro connector.
  While the exact number power capacity (i.e. 26800mAh) is not that important,
  it is nice to have at least 2 3A outputs.
  Since some these battery packs do not come with a complete set of charging cables,
  it may be necessary to purchase additional cables.
  In general, the HR2 does not need long cables.
  Also, when the battery first pack shows up,
  be sure to charge it up  since it takes a while to charge these battery packs.

* USB-A to USB-C Cable:
  The robot is powered via a USB-A to USB-C cable.
  Shorter cables are desirable (6in/15cm) to (12in/30cm).
  The theory was that all USB cables with the correct connectors on the end would "just work".
  In practice, the marketplace has learned to economize by creating specialized "power" cables
  which are slightly less expensive to manufacture.
  Thus, take any cable that is the correct length and do not worry about whether is says "power" or not.

For bringing up the Raspberry Pi 4, it is frequently useful to have some additional hardware.
The hardware is listed below is primarily used for bringing up WiFi on the Raspberry Pi 4.
For completeness, the hardware is listed here, but its usage is discussed more completely
in the [Robot Computer Ubuntu Installation](#robot-computer-ubuntu-installation) section
of this document.
Be sure to read about [keyboard/display vs. headless](#robot-computer-ubuntu-installation) configuration
before purchasing any of the hardware immediately below:

* HDMI Display (for keyboard/display based configuration):
  The resolution does not particularly matter.
  The only requirement is that it has a standard sized HDMI input jack.

* Micro-HDMI to regular HDMI adapter cable (for keyboard/display based configuration):
  The Raspberry Pi 4 has 2 micro HDMI connectors.
  This cable adapts between the Raspberry Pi 4 micro-HDMI connector
  and the regular display HDMI connector.

* USB-A Keyboard (for keyboard/display based configuration):
  This is needed to type commands into the Ubuntu console.

* RJ45 Ethernet Cable (for "headless" based configuration):
  It is counter-intuitive, but this is very useful for bringing up the Raspberry Pi 4 WiFi.

The list above should be a pretty complete list of the required additional hardware.

### Development Computer Ubuntu 20.04 Install

The development computer is assumed to be running Ubuntu 20.04.
It is beyond the scope of this document explain how to download Ubuntu 20.04.

You may do one of the following:

* Purchase a laptop with Ubuntu preinstalled.

* Install Ubuntu 20.04 onto an 64-bit x86 processor yourself.

* Install Ubuntu 20.04 to run under a virtualization environment
  like (VirtualBox)[https://www.virtualbox.org/].)
  If you use VirtualBox, be sure to configure the Ethernet adapter to be in "bridged mode".
  Other than that, just follow the lengthy installation instructions.

### Development Computer ROS2 Install

Once you have Ubuntu 20.04 installed, please install the ROS2 version named
[Foxy](https://index.ros.org/doc/ros2/Installation/Foxy/) which configured for Ubuntu 20.04.
Do a full desktop install.

### Development Computer Configuration:

This is where various specialized configurations occur.
For now there is only one:

* [Install `usbip` Client Service](#install-usbip-client-service):
  The `usbip` protocol is used to allow the development computer to connect to the ST-Link
  on the robot micrcontroller.

#### Install `usbip` Client Service

The robot microcontroller has an ST-Link system on it that is used for firmware download and debug.
The robot microcontroller firmware is developed on the development computer.
The robot computer provides a bridge between the ST-Link on the robot microcontroller
and the development computer as shown immediately below:

                            IP                    USB
     Development Computer <====> Robot Computer <=====> Robot Microcontroller
        (usbip client)            (usbip host)

The protocol is called `usbip` for USB Internet Protocol.
This protocol enables the access to USB devices on other computers as if they are local.

<!-- Are the correct packages already installed? -->

Create a systemd service file:

     sudo -s   # switch over to super user
     cat <<EOF > /etc/systemd/system/usbip-client.service
     [Unit]
     Description=USB/IP Client Modules

     [Service]
     Type=oneshot
     RemainAfterExit=true
     ExecStart=/sbin/modprobe -qab vhci-hcd

     [Install]
     WantedBy=multi-user.target
     EOF

     exit # Exit super user mode

     systemctl enable usbip-client.service
     systemctl start usbip-client.service 
     systemctl status usbip-client.service  # Should be OK

     # Verify that it worked:
     lsmod | grep vhci
     # Should list two lines

### Development Computer STM32CubeIDE Install

There are multiple cross platform IDE's (Integrated Development Environment) out there.
The `STM32CubeIDE` IDE is selected because it is directly supported by microcontroller vendor
(i.e ST Microelectronics.)
There are others (e.g. `vscode`, `Keil`, etc.) that could work as well,
but they are not directly supported by STM.

Please note that these instructions are for STM32CubeIDE 1.5.x.
The 1.6.x version of STM32CubeIDE has been released and these install instructions
need to be updated.

Please do the following:

1. Uninstall Notes:

   Note that `STM32CubeIDE` is a big complicated program
   that feels obligated to create a bunch of sub-directories in your home directory.
   At this point in time, the following sub directories are created:
 
   * `.stm32cubeide/`:
     It seems to just contain `favorites.mcus.txt`.

   * `.stm32cubemx/`:
     Some `plugins/` and `thirdparty/` software.

   * `.stmcube/`:
     Empty!

   * `.stmcufinder/`:
     Some `plugins/`.

   * `st/`:
     This s a sub-directory that contains the actual unpacked IDE files
     from the download `.zip` file (see below.)

   * `STM32Cube/`:
     This is a huge sub-directory contains many gigabytes of files.
     It sometimes downloads new updates that essentially duplicated the contents
     of the `st/` directory.

   * `STM32CubeIDE`:
     This is the default sub-directory for your workspace (see further below.)

   If you ever need to clean `STM32CubeIDE` off your computer, delete all of these sub-directories.
   With the exception of the `st/` sub-directory,
   all of the other directories are created the first time you run `STM32CubeIDE`

2. Notation:

   Downloading the `STM32CubeIDE` is pretty involved.
   In the instructions below, the following notation in all capital letters shows up:

   * USER:
     This is your user name (e.g. `alice` for `/home/alice`).

   * PASSWORD:
     This is your login password.  It is needed for the `sudo` program.

   * X:
     The major version of the `STM32CubeIDE`.

   * Y:
     The minor version of the `STM32CubeIDE`.

   * D:
     Decimal digits that changes from release to release.

3. Enable `sudo` command:

   Run the `groups` command and verify that you are in the `sudo` group.
   If `sudo` is not present, you are not `sudo` enabled.
   Please visit
   [How to Add User to Sudoers](https://phoenixnap.com/kb/how-to-create-sudo-user-on-ubuntu).
   You can probably skip step 1, since you probably already have a user account.

4. Create STM Account:

   Visit the
   [STMe2CubeIDE download page.](https://www.st.com/en/development-tools/stm32cubeide.html).

   Basically, you ***MUST*** create an account with ST before you can get the software.
   Create your account now, if you do not already have one.
   Fill in the forms and wait for the account to happen.
   STM will offer the you the wonderful opportunity to let them send you lots of marketing,
   but they also give you the opportunity to decline this generous offer.

5. Download and Save `.zip` File:

   Now that you have the STM account, STM will let you download the software.
   Revisit,
   [STMe2CubeIDE download page.](https://www.st.com/en/development-tools/stm32cubeide.html),
   and click on the `[Get Software]` button for the `STM32CubeIDE-Lnx` Generic Linux installer.
   The instructions below are for the Generic Linux installer, **NOT** the Debian installer.

   Eventually, you will get your hands on a `.zip` file with a long ugly name
   that looks basically like this:

     en.st-stm32cubeide_1-X-Y_DDDD_DDDDDDDD_DDDD_amd64_sh.zip

   Please store the `.zip` file someplace, just in case you need to reinstall in the future.

6. Unzip the Downloaded `.zip` file:

   Now, unzip the file using the command immediately below:

     unzip -x en.en-st-stm32cubeide_1-X-Y_DDDD_DDDDDDDD_DDDD_amd64_sh.zip

   This should result in a `.sh` (shell) file that looks kind of like:

     st-stm32cubeide_1.X.Y_DDDD_DDDDDDDD_DDDD_amd64.sh

   The version information is always changing, so the X, Y, and D values change regularly.
   This is the unzipped installer file.

7. Execute the Installer script file: 

   It is going to ask you agree to a whole bunch of license agreements,
   install stuff in places, etc.
   There are also a few steps that need to be done in super user mode.

   Now execute the install script file:

     sh st-stm32cubeide_1.X.Y_DDDD_DDDDDDDD_DDDD_amd64.sh

   Roughly speaking the following output occurs.
   It will change over time, so do not be concerned if it looks a little different.
   You input response are marked with `<== ...`:

        Verifying archive integrity... All good.
        Uncompressing STM32CubeIDE 1.X.Y installer  100%
        STMicroelectronics Software License Agreement
        ...   <== Big long license agreement.  Type [Space] to scroll through it.
        I ACCEPT (y) / I DO NOT ACCEPT (N) [N/y]                        <== Type 'y'
        License accepted.
        Do you want to install STLinkServer and Udev rules for STLink and Jlink?
        Without these packages, you will not be able to use debugging feature.
        Install them? (you need sudo permission to do that) [Y/n]       <== Type 'Y'
        STM32CubeIDE install dir? [/home/HOME/st/stm32cubeide_1.X.Y/]   <== Type [Enter]
        Installing STM32CubeIDE into ...
        Java cacerts symlinked to /etc/ssl/certs/java/cacerts
        [sudo] password for USER:                                       <== Type your PASSWORD
        Creating directory root
        Verifying archive integrity... All good.
        Uncompressing STM udev rules installer  100%
        STMicroelectronics Software License Agreement
        ...   <= Big long license agreement.  Type [Space] to scroll through it
        I ACCEPT (y) / I DO NOT ACCEPT (N) [N/y]                        <== Type 'y'
        STMicroelectronics Software License Agreement
        ...   <== Another long license agreement.  Type [Space] to scroll through it
        I ACCEPT (y) / I DO NOT ACCEPT (N) [N/y]                        <== Type 'y'
        License accepted.
        stlink-server v2.Z.Z (ZZZZ-ZZ-ZZ-ZZ:ZZ) installation started.
        ...  <== More text that can be ignored.
        Do you want to install Segger J-Link udev rules? [Y/n]          <== Type 'n'
        STM32CubeIDE installed successfully

8. Put `stm32cubeide` in your PATH:

   Using your favorite text editor (e.g. `nano`),
   add the following to your `~/.bashrc` file near the bottom of the file:

     export PATH=$PATH:$HOME/st/stm32cubeide_1.X.Y/stm32cubeide

   Remember to use the correct values for X and Y.
   Now `source` the `~/.bashrc` file as follows:

       source ~/.bashrc

   The command:

        which stm32cubeide

   should return `/home/USER/st/stm32cubeide_1.X.Y/stm32cubeide`.
   If it does, you have successfully installed stm32cubeide.

It program is run for the first time further below in the
[Firmware Development](#firmware-development) section.
That concludes `STM32CubeIDE` software installation.

### Robot Computer Ubuntu Installation

This section is broken into the following sub-sections:

* [Command Line Notation](#command-line-notation):
  This briefly discusses the command-line notation rules used.

* [Bring Up Strategy](#bring-up-strategy):
  This discusses the two initial bring up strategies.
  You get be pick between display/keyboard bring up vs. headless bring up.

* [Install Ubuntu onto a Micro-SD Card](#install-ubuntu-onto-a-micro-sd-card):
  A program called `rpi-imager` installed onto your development computer and
  is used to load the Ubuntu image for the Raspberry Pi4 onto a micro-SD card.

* [Raspberry Pi 4 Connector Locations](#raspberry-pi-4-connector-locations):
  This section describes the names and locations of the various Raspberry Pi 4 connectors.

* [Initial Bring Up](#initial-bring-up):
  The Raspberry Pi 4 is powered up to the point that it can be logged into.
  This is easy if you have a keyboard and display plugged into the Raspberry Pi 4
  and it is significantly more difficult if you are not.

* [Login and Configuration](#login-and-configuration):
  This takes you from login up to the point where is ready to do actual software development.

* [Remote USB Installation](#remote-usb-installation)
  Remote USB is used to provide access to the ST-Link on the robot mircocontroller.
  Code must be installed on both the robot computer (and the development computer.)

#### Command Line Notation

Most of the configuration is done via typing in commands to a console interpreter
(i.e. a Linux shell.)
When you see block of code like:

     # Example comment
     echo hello
     # `hello` should show up.
     
Just type in the code one line at a time to the console.
All characters after from sharp character (`#`) onward are a comment that does not need to be typed in.

Also, you will see some upper-case keywords in the scripts below.
You should substitute the values you choose for these keywords into the scripts below.
For example, when you `NEWHOSTNAME` you substitute in the new host name that you selected
(e.g. `myrobot`, `fun4me`, etc.)

These are the current upper-case substitutions:

* `NMAP_IP_RANGE`:
  This is a special internet protocol address that is used by the `nmap` program.
  This is for the headless install option only.

* `RPI4_NET_ADDRESS:
  This is a 4 decimal numbers separated by periods (`.`).
  This is the initial internet address of the robot.
  This instruct

* `NEWHOSTNAME`:
  The original host name provided by the downloaded Ubuntu image is `ubuntu`.
  This needs to be changed.

* `NEWUSERNAME`:
  This is a new user account name that you select.
  Many people just use their first name (e.g. `alice`, `bob`, `carol`, `dave`, etc.)

#### Bring Up Strategy

For the HR2, the nominal computer for the Robot Computer is a Raspberry Pi 4 with at least 4GB.
If necessary,
reread the [introduction](#introduction) to refresh your memory of what the robot computer is.

There are two installation strategies:

* Display/Keyboard:
  The display/keyboard method is the easiest, but it requires:

  1. Keyboard:
     A Keyboard with a USB-A connector is plugged into one of the USB ports on the Raspberry Pi 4.

  2. HDMI display:
     While resolution does not matter, having the HDMI input connector is required.

  3. Micro HDMI to regular HDMI cable:
     This cable adapts between the Raspberry Pi 4 and the HDMI cable.

* Headless:

  A computer without a keyboard/display is called "headless".
  It can only be administered via a network connection.
  For this method, the Ethernet cable is temporarily required.
  One end of the Ethernet cable is plugged into the Raspberry Pi 4 and
  the other end is plugged into your local area network.
  This is done with a RJ45 cable.
  If you normally use WiFi, you may have to search for the RJ45 connector on your cable modem.
  If you can not find a live RJ45 connector to plug into, you must use the display/keyboard method.

#### Install Ubuntu onto a Micro-SD Card

The instructions here are based on 
[Ubuntu Install](https://ubuntu.com/tutorials/how-to-install-ubuntu-desktop-on-raspberry-pi-4).
Since web pages change all the time, the steps are summarized below:

1. Install `rpi-imager`:
   Run the following command to install `rpi-imager`:

     `sudo apt install -y rpi-imager`

2. Install Micro-SD Card into the computer:
   Install the 32GB (or larger) micro-SD into the micro-SD card adapter.
   Insert the micro-SC card adapter into your development computer.
   If you are running Ubuntu under a virtual machine (i.e. VirtualBox).
   it may be necessary to import the micro-SD card into the virtual environment.
   Once the card is installed, dismiss any pop-up windows that show up.

3. Run `rpi-imager`:
   Type `rpi-imager` and a window should pop with 3 buttons on it.
   The first two buttons are `[Choose OS]` and `[Choose SD Card]`.
   The third button is a grayed out `[Write]` button.
   
5. Choose OS:
   These windows change from time-to-time, so the instructions below may get a little out of date.

   1. Click on `[Choose OS`].

   2. Select `[Other general purpose OS]`.

   3. Select `[Ubuntu]`.

   4. Scroll down to `Ubuntu Server 20.04.X LTS (RPI 3/4/400)`.
      This is the `64-bit server OS with long term support for arm64 architectures`.

6. Choose SD Card:

   It is extremely likely that only one card will be available.
   A 32GB micro-SD card might show up as 31.9 GB.
   Click on it.

7. Write the Card:

   The `[Write]` button should no longer be grayed out.
   Click on it.
   Click on `[YES]` in the pop-up.
   It may ask for your password, type it in and click `[OK]`.
   You may click on `[CANCEL WRITE]` at any time, but you will have to start all over again.
   This should take a few minutes.

8. Wait a while for the download to occur:
   While waiting, please remember that there are additional steps required,
   so do not unplug the micro-SD card adapter when you are done.
   When the `rpi-imager` is done, it will say `remove the SC card from the reader`.
   Do not remove the adapter,
   but do click on `[Continue]`

9. Close `rpi-imager`:
   Dismiss the `rpi-imager` program by click on the `[X]` in the upper right corner.

10. Remove the micro-SD card.

#### Raspberry Pi 4 Connector Locations

Before getting started please familiarize yourself with the locations of Raspberry Pi 4 connectors.

First, orient the Raspberry Pi 4 so that the 40-pin connector (2 rows of 20 pins)
is on top and to the left.

Now find the following connectors:   

   * RJ45 Ethernet connector:
     This is located on the right edge in the upper right.

   * 4 USB type A connectors:
     These are located on the right edge under the RJ45 ethernet connector.
     There are two USB connector in each of the two silver "bricks" under the RJ45 connector.

   * USB C Power Connector:
     The USB C connector is on the bottom edge to the far left.

   * 2 Micro HDMI Connectors:
     On the bottom edge, the two micro HDMI connectors are to the right USB C power connector.

   * 1 Micro-SD Card connector:
     On the left edge, but underneath the board you find the micro-SD card.

   * Red Power LED:
     There is a red power LED near the USB C Power Connector.
     It is the very small component on the left edge at the very bottom
     nearest the bottom left mounting holes
     You can not tell that it is red by looking at it.
     Just be aware that this component will light just as soon as power is applied
     to the Raspberry Pi 4.

   * Green Activity LED:
     There is a green activity LED immediately above the red power LED.
     Again, you can not tell that it is green.
     All you need to know is that it is there and turn on and off as various activies
     occur on the Raspberry Pi 4.

As a further note, there is no on/off switch on the Raspberry Pi 4.
What this means that as soon as the "power cable" is connected
between the battery pack and the Raspberry Pi 4, the Raspberry Pi 4 will probably start.
Do not plug in any power cable until explicitly told to do so in the instructions below.

While the Raspberry Pi does not have an on/off switch,
some battery packs do have an on/off switch.
So depending upon your battery pack, you may have to toggle a batter power switch to provide power.
Once power is applied, the Red Power LED will light up immediately and
the green activity LED will start to randomly turn on and off as the Ubuntu operating system powers up.
In addition, if a display is both powered up and connected,
it will start to display text on power up.

Please reread section on [keyboard/display vs headless install](robot-computer-ubuntu-installation).
Please follow the instructions for either
[Keyboard/Display Installation](#keyboard-display-installation) or
[Headless Installation](#headless_installation).

#### Initial Bring Up

This is where the initial Raspberry Pi 4 power up occurs.
This takes you as far as the `login:` prompt.

Perform the instructions below depending upon which [bring-up strategy](#bring-up-strategy) you selected:

* [Keyboard/Display Bring Up](#keyboarddisplay-bring-up)
  Perform these instructions for the keyboard/display power-up method.

* [Headless Bring-up](#headless-bring-up):
  Perform these instructions for the headless bring-up method.

##### Keyboard/Display Bring-up

For keyboard/display installation do the following:

1. Plug in keyboard:
   Plug your keyboard into one of the USB type A connectors.

2. Plug in micro HDMI-Cable:
   Plug one end of the micro-HDMI cable into either one of the Raspberry Pi 4 micro-HDMI connectors.

3. Plug into the HDMI Display:
   Plug the other end of the micro-HDMI cable into your HDMI display.

4. Plug micro-SD Card:
   Plug in the micro-SD card

4. Display Power Up:
   Turn on the HDMI display.

5. Before Power Up:
   Remember, once the power cable is connected,
   the Raspberry Pi will power up immediately since there is no on/off switch.
   
6. Connect Power Cable and Power Up:
   Make sure you have a cable that is compatible between your battery pack and
   the USB-C connector on the Raspberry Pi 4.
   Your battery pack probably came with one, so plug it in and watch the show.

7. When your display shows something with something like `ubuntu login:` it means you are ready to login
   and start configuring the Raspberry Pi.
   You can skip the section immediately below on headless install.

Proceed to the [Initial Bring up](#initial-bring-up) section.

##### Headless Bring-up

This section concerns headless install which is significantly more complicated than the headless 
The overall goal of a headless install is to login into the Raspberry Pi 4 remotely
via the internet.

What makes headless installation harder is that when the Raspberry Pi connects to the internet
for the very first time is it will ask the network to give it an internet address
via a protocol call DHCP -- Dynamic Host Configuration Protocol.
We need to figure out what address was assigned by DHCP
*before* you can log into the Raspberry Pi 4 from the development computer.

<!-- link to `ip` info: https://packetpushers.net/linux-ip-command-ostensive-definition/ -->

Please perform the following steps:

1. Install the following packages on your development computer:

   Install the following packages onto your computer:

        sudo apt install -y iproute2               # Get `ip` command
        sudo apt install -y nmap                   # Get `nmap` local net scanner.
        sudo apt install -y net-tools              # Get `arp` command, ping, ifconfig, etc.
        sudo apt install -y libnss-mdns mdns-scan  # For avhi (i.e. zero-conf)

   For you information:
   * The `ip` command is used to flush something called the ARP cache.
     ARP stands for Address Resolution Protocol.
   * The `nmap` command scans your local internet looking for active internet addresses.
   * The `arp` command lists all of the active internet addresses.
   * The `libmss-mdns` and `mdns-scan` packages provide functionality loosely called
     [zero-configuration networking](https://en.wikipedia.org/wiki/Zero-configuration_networking)
     or "zero-conf" for short.
     This allows us to login into a computer using its host name instead of a bunch of numbers.

2. Verify zero-conf is working:

   Run the following command:

        ping -c 3 `hostname`.local  # Note that the accent ("`") is used instead of the single quote ("'").
     
   It should print out a few lines as follows:
   
        PING ??? (192.168.xxx.yyy) ...

   There are three internet address ranges that are reserved for local area networks.
   * Class A: 192.168.yyy.zzz where yyy is normally 1 (i.e. 192.168.1.zzz).
   * Class B: 169.124.yyy.zzz.
   * Class C: 10.xxx.yyy.zzz, where xxx is typically 1 (i.e. 10.1.yyy.zzz).
   * Something else: These headless instructions will not work;
     use a keyboard/display install.

   For the `nmap` command, you will need to specify an address space range to scan.
   Please use the following:
   * Class A: 192.168.yyy.0-255 where yyy is the number from you ping.
   * Class B: 169.124.0-255.0-255 .
   * Class C: 10.xxx.0-255.0-255  where xxx is from your class C network.
   This is called NMAP_IP_RANGE below:

   These instructions will usually work for class A and class B networks,
   but will frequently fail for class C networks.

3. Determine the currently used internet addresses:

   Run the following commands:
   
        sudo ip neigh flush all     # Flush arp cache *BEFORE* powering up RPi4
        sudo nmap -p ssh -n NMAP_IP_RANGE  # Class A is ~10 seconds, others are about ~5 minutes.
        arp > /tmp/before.arp

4. Connect network cable:
   Plug one end of your RJ45 cable into the raspberry Pi and the other into your local network.
   
5. Before Power Up:
   Remember, once the power cable is connected,
   the Raspberry Pi will power up immediately since there is no on/off switch.
   
6. Connect Power Cable and Power Up:
   Make sure you have a cable that is compatible between your battery pack and
   the USB-C connector on the Raspberry Pi 4.
   Your battery pack probably came with one, so plug it in and watch the show.

7. Wait for 2 minutes:
   After these 2 minutes the Raspberry Pi should be up and running.

8. Rescan for currently used internet addresses:
  
   Run the following commands:
   
        sudo ip neigh flush all   # Flush arp cache *BEFORE* powering up RPi4
        sudo nmap -p ssh -n NMAP_IP_RANGE  # Class A is ~10 seconds, others are about ~5 minutes.
        arp > /tmp/after.arp     # Note this time `after.arp` is being used instead of `before.arp`

9. Find the new internet address:

   Run the following command:

        diff /tmp/before.arp /tmp/after.arp

   This should have on line that shows up that is the internet address of your Raspberry Pi 4.
   Call this RP4_NET_ADDRESS

10. Make sure Raspberry Pi 4 is alive:

         ping -c 3 RP4_NET_ADDRESS

    If you gets some output.
    If not, the RP4_NET_ADDRESS you have is not connected to your Raspberry Pi 4 computer

11. Use `ssh` to log into your Raspberry Pi 4:

    Run the following command.

         ssh ubuntu@RP4_NET_ADDRESS

    It might probably complain about a fingerprint issue.

    Please use the "yes" option.

    Sometimes it will complain about `REMOTE HOST IDENTIFICATION HAS CHANGED!`
    It will printout something:

        remove with:
	ssh-keygen -f "/home/YOUR_ACCOUNT/.ssh/known_hosts -R "AN_IP_ADDRESS"

    Just run the command and try the `ssh ubuntu@RPI_NET_ADDRESS` again.

12. Wait for login prompt:

    If everything worked right, you should get a login prompt
    
        ubuntu login:

    Headless login appears to have largely succeeded.

    It is now time to proceed to the next section immediately below.

#### Login and Configuration

This section takes you from the `login:` prompt to more complete Raspberry Pi configuration.

The basic steps are as follows:

1. [Change the Login Password](#change-the-login-password):
   The initial password is `ubuntu`, but the system forces you to change it to something else.

2. [Change the Host Name](#change-the-host-name):
   It is important the change the host name from `ubuntu` to something else.

3. [Create a New User Account](#create-a-new-user-account):
   It is useful to create a new user account with `sudo` access.

4. [Set Up Zero Configuration](#set-up-zero-configuration):
   This allows you to be able to connect to the robot with the robot name.

5. [Login into Robot from Development Computer](#login-into-robot-from-development-computer):
   Now you should be able to login to the computer from your development computer.

6. [Configure Wifi](#configure-wifi):
   Configure your WiFi access.

7. [Remote USB Installation](#remote-usb-installation):
   This configures a system call `usbip`
   for remote access to the ST-Link device on the Robot Microcontroller.

8. [Final Configuration Notes](#final-configuration-notes):
   Some final comments on configuration.

##### Change the login password:

When you first login, the system will insist that you change the password for the `ubuntu` account.
It will prompt you for the initial password (`ubuntu`) first, followed by your new password two times.
The reason for prompting for the new password two times is just in case there is a typo.
Upon success, the Raspberry Pi 4 will disconnect.
You have successfully changed the password.

You will have to login again.
On for the headless bring-up method,
this will require that you run the `ssh ubuntu@RPI_NET_ADDRESS` command again.
It should prompt for a password and just type in the new password.

When you are done with this step the password should be changed and
you should be logged into the Raspberry Pi 4.
You should get prompt that looks like `ubuntu@ubuntu:~$`.

##### Change the Host Name:

Right now you host name should be `ubuntu`.

If you type `hostname`, it should return `ubuntu`.
This verifies that the host name is still `ubuntu`.

It is important to change the host name to something other than `ubuntu`.
The reason why is because it is necessary to get each robot a unique name
to make it easier to connect to it.
If all robots were named `ubuntu`, you would have to keep typing the annoying internet address
(e. g. 192.168.1.yyy`) instead.

Please come up with a fun new host name.
It should be lowercase letters and digits only, with no punctuation
(`alice`, `robot4all`, `go2dance`, etc.)
In the command below `NEWHOSTNAME` is used in the commands,
please substitute your lowercase letters and digits for `NEWHOSTNAME` below:

Run the following commands:

     sudo hostnamectl set-hostname NEWHOSTNAME
     # The prompt should change to `ubuntu@NEWHOSTNAME:$`
     hostname
     # You should get back `NEWHOSTNAME`

##### Create a New User Account:

You are welcome to continue using the `ubuntu` account the Raspberry Pi 4,
but most people try to create their own personal accounts.
Most people make their account names all lower case letters with no numbers or punctuation
(`greatfun`, `fred`, etc.)

In the script below, substitute your new account name for `NEWUSER`:
   
     sudo adduser NEWUSER
     # Type in new password once
     # Type in the same password again
     # Fill in the remaining information.
     # Type `Y` when it asks `Is the information correct?

Give the new account super-user capability with the following command:

     sudo usermod -aG sudo NEWUSER
     sudo usermod -aG dialout NEWUSER

<!--
Issue: It did not set default directory to /home/NEWUSER .
-->

Now verify the user account with the commands below:

     su NEWUSER
     # Type in password
     # The prompt should change to `NEWUSER@NEWHOSTNAME@:~$`
     whoami
     # It should respond with NEWUSER
     sudo echo hello
     # It should prompt for the password again follow by `hello`
     exit

##### Set up zero configuration.

Zero configuration is a way to export your host name make it easily accessible
from you development computer.
This means you will no longer have to type in obscure numbers.

First, install some zero configuration packages with the command below:

     sudo apt install -y net-tools libnss-mdns mdns-scan

Now, verify that it works with the following command:

     ping -c 3 NEWHOSTNAME.local
     # You should get back several lines of code.

Now logout as follow:

     exit  # Force a logout

##### Login into Robot from Development Computer

It should be very easy to log into robot computer from your development computer:

     ssh NEWUSER@NEWHOSTNAME.local
     # It may complain about authenticity problems.
     # If so, run `ssh-keygen -f ...` command and try the `ssh NEWUSER@NEWHOSTNAME.local` again.
     # If it complains about fingerprints, type `Y`.
     # Type in the password.
     # You should get a prompt of `NEWUSER@NEWHOSTNAME@hr2b

<!-- Consider doing a `sudo apt update && sudo apt upgrade` -->

##### Configure Wifi

The next step requires access to a WiFi router connected to your local network.

<!-- https://kifarunix.com/connect-to-wifi-in-linux-using-nmcli-command/  -->

1. Install network manager:

        sudo apt install -y network-manager   

   You now have a program named `nmcli` (Network Manager Command Line Interface).

2. Verify WiFi is enabled:

   To verify that the wifi is enabled do the following:

        nmcli radio wifi
        # It should come back with `enabled`.
        # If `disabled` run `nmcli radio wifi on`

3. Search for WiFi access points with the the following command:

        nmcli dev wifi list
        # A list of WiFi access points should show up.

   The name of the access point is called an `SSID`.
   Find the SSID of the WiFi access point to connect to.
   In the scripts, below substitute the correct name for SSID.

4. Register a Wifi access point for logging in with the following command:

       sudo nmcli --ask dev wifi connect SSID
       # Type in your `sudo` password if prompted.
       # Type in WiFi password after the password prompt.

5. Verify active connection with the following command:

       nmcli con show --active

  You should see one active connection.

6. Run `ifconfig` (Interface Configure):

       ifconfig

   You should get network status for `eth0`, `lo`, and `wlan0`.
   `eth0` is the hardwired ethernet.
   `lo` is a  LOopback pseudo interface.
   `wanl0` is the wireless (WiFi) interface.
   Just in case, write down `inet` address.
   You can ignore the `netmask` and `broadcast` fields.

7. Reboot and Unplug Ethernet Cable with the following commands:

       sudo reboot -h now  # Force an immediate reboot
       # Now unplug the ethernet cable (for the headless bring up strategy)
       # Wait a for a couple of minutes

8. From your development computer, verify that the robot computer logged into the WiFi access point
   with the following command:

       ping -c 3 NEWHOSTNAME.local
       # You should get 3 ping responses

9. Login/logout to/from the robot computer with the following commands:

       ssh NEWACCOUNT@NEWHOSTNAME
       # Type in password for prompt
       # When logged in shut down Raspberry Pi 4
       sudo halt
       # Type in password for prompt
       # The robot should turn off

##### Remote USB Installation

The robot microcontroller has an ST-Link system on it that is used for firmware download and debug.
The robot microcontroller firmware is developed on the development computer.
The robot computer provides a bridge between the ST-Link on the robot microcontroller
and the development computer as shown immediately below:

                            IP                    USB
     Development Computer <====> Robot Computer <=====> Robot Microcontroller
        (usbip client)            (usbip host)

A system called `usbip` is used to provide remote access to USB devices.
A `usbip` client is installed on the development computer and a `usbip` host is installed
on the robot computer.
When `usbip` properly installed, the development computer accesses the remote ST-Link subusystem
as if it was locally plugged into the development computer.

This section discusses how install `usbip` on the robot computer.
It is broken into the following sections:

* [Install `usbip` Packages](#install-usbip-packages)

* [Install `usbip` Service](#install-usbip-service)

* [Verify `usbip` Installation](#verify-usbip-installation)

###### Install `usbip` Packages

Install the following packages:

     sudo apt install -y linux-tools-common
     sudo apt install -y linux-tools-raspi
     sudo apt install -y usbutils
     sudo apt install -y linux-cloud-tools-common  # Not sure about this one (seems to help)

Install the following symbolic link:

     sudo ln -s /usr/share/misc /usr/share/hwdata  # Only need to do once

The symbolic link deals with the fact that the USB ids file got moved from `/usr/share/hwdata`
to `/usr/share/misc`.
It is much easier to fix this problem with a symbolic link than it is to fix the code.

Once you have installed the packages and symbolic link, verify that everything is installed.

    which usbip   # Should return `/usr/bin/usbip`   # This is the `usbip` user level program
    which usbipd  # Should return `/usb/bin/usbipd`  # This is the `usbip` daemon.

###### Install `usbip` Service

The Robot computer needs to do three things on start-up.

1. Load a couple of kernel modules -- `usbip-core` and `usbip-host`.

2. Start the `usbipd` daemon.

3. Find the ST-Link and make it available for remote access.

This is done with two files:

* `/etc/systemd/system/usbip-host.service`:
  This is a `systemd` unit file that properly installs the kernel modules
  and runs the daemon.
  It also invokes the `usbip-host.service.sh` shell file immediately below.

* `/usr/local/bin/usbip_host.service.sh`:
  This determines if an ST-Link plugged into one of the robot computer USB ports and
  (if present) bind it such that it is available for external access.
  
The file is installed as super user:

     sudo -s  # If prompted for a password, type it in.
     # Prompt character changes from `>` to `#` to remind you that your are super-user

Now install `/etc/systemd/system/usbipd.service` as follows:

     cd /etc/systemd/system
     wget https://raw.githubusercontent.com/hbrobotics/hbrc_ros_robot_platform/master/bin/usbip_host.service

Now install `/usr/local/bin/usbip_host.service.sh` as follows:

     cd /usr/local/bin
     wget https://raw.githubusercontent.com/hbrobotics/hbrc_ros_robot_platform/master/bin/usbip_host.service.sh
     chmod +x usbip_host.service.sh

###### Verify `usbip` Installation

Plug a USB-A to USB-micro cable between the Robot Computer and the Robot Microcontroller
(i.e. the Nucleo.)

Verify that both files exist:

     ls -l /etc/systemd/system/usbip_host.service  # Should print a one line directory listing
     ls -l /usr/local/bin/usbip_host.service.sh   # Should print a one line directory listing

Now enable/start the service:

     systemctl enable usbip_host.service
     systemctl start usbip_host.service

Verify that it is running:

     systemctl status usbip_host.service
     # A bunch of stuff should print out.  "Active: active (running) ..." is want is wanted.
     
Verify that it can find the ST-Link module:

     usbip list -l
     # It should print out `busid ...` followed by `STMicroelectronics ...`
     # If not, try to reboot.

Verify that it remotely accessible:

     usbip list -r localhost
     # Should print out `localhost`, followed by the same lines as imediately above.
     # If not, try to reboot.

Now exit super-user mode:

     exit

Things are looking good.
Now comes the final test where the Robot computer is rebooted and accessed remotely
from the development computer.

Force the Robot Computer to reboot.
     
     sudo reboot -h now
     # If you are logged via remote shell, you will be immediately logged out.

Wait 2 or 3 minutes for the Robot Computer to reboot.
While you are waiting do the following in a console window on the deveopment computer:

     export HR2_REMOTE=NEWHOSTNAME.local
     # This sets the HR2_REMOTE environment variable to be the robot host name followed by `.local`.
     
After the 2 or 3 minutes have elapsed, you should be able to ping the Robot computer:

     ping -c 3 $HR2_REMOTE
     # You should get 3 ping messages.

If that does not work you can try to run the following commands:

     sudo ip neigh flush all   # Flush arp cache *BEFORE* powering up RPi4
     sudo nmap -p ssh -n NMAP_IP_RANGE  # Class A is ~10 seconds, others are about ~5 minutes.
     arp

Once `ping` is working, do the following:

     usbip list -r $HR2_REMOTE
     # Should get the pretty much listing as when this command was run on the Robot computer.

That is pretty much it.
Eventually, when the firmware development software is ready for use,
the `.../bin/xstm32cubeide` wrapper is used to access the ST-Link remotely
from the development computer.

<!-- USBIP Notes:

`usbip` is a protocol for connecting 

There are USBIP two articles that the information below is derived from:

* [Linux Magazine](https://www.linux-magazine.com/Issues/2018/208/Tutorial-USB-IP)

* [Stack Overflow](https://unix.stackexchange.com/questions/528769/usbip-startup-with-systemd)

* [RPi](https://community.home-assistant.io/t/rpi-as-z-wave-zigbee-over-ip-server-for-hass/23006)

* [Cern CentOS usbip](https://clouddocs.web.cern.ch/advanced_topics/share_usb_devices.html)
Some commands:

     # On robot computer:
     # Do once
     sudo apt install linux-tools-common
     sudo apt install linux-tools-raspi
     sudo apt install usbutils
     sudo apt install linux-cloud-tools-common  # Not sure about this one (seems to help)
     sudo ln -s /usr/share/misc /usr/share/hwdata  # Only need to do once

     # Do on reboot:
     # Note that usbipd is in /usr/bin/usbipd  not  /usr/sbin/usbipd
     sudo modprobe usbip-core  # Not needed
     *sudo modprobe usbip-host
     *lsmod | grep usbip
     *sudo usbipd -D  # Start usbip daemon
     *netstat -tnlp | grep 3240  # Verify daemon is runnning
     usbip list -l  # Should list usb ports
     sudo usbip bind -b BUS_NAME  # 1-1.3 (for example)

     # On development computer:
     *sudo modprobe vhci_hcd
     *sudo modprobe usbip_core
     sudo usbip list -r hr2b.local  # Should show avail devices (there is only one exported for now)
     sudo usbip attach -r hr2b.local -b BUS_NAME
     lsusb | grep -i stm

     # Detaching
     sudo usbip port  # lists ports in use
     # Prints out each port binding.  
     sudo usbip detach -p 00  # Note that the port number is a string, not a number
     lsusb | grep -i stm   # no match

     # Unbind on the robot computer (Really quite optional)
     sudo usbip unbind -b 1-1.3 # (for example)

-->

##### Final Configuration Notes

In general, configuration basically never ends.
But this is a reasonable place to stop for now.
The next major step is to install ROS2 on the robot computer

### Robot Computer ROS2 Installation

The initial installation of ROS2 is pretty straight forward.
The steps are:

1. [Connect to ROS2 PPA](#connect-to-ros2-ppa):
   The ROS2 organization maintains its own PPA (Personal Package Archive).

2. [Download ROS2 Foxy](#download-ros2-foxy):
   The latest ROS2 release is called "Foxy".

3. [Final ROS2 Configuration](#final-ros2-configuration):
   The final ROS2 configuration is pretty simple.

#### Connect to ROS2 PPA

The ROS2 instructions for connecting to the ROS2 PPA are a little more involved
than the instructions immediately below.
The instructions use `apt-key` rather than `curl`:

     sudo apt-key adv --fetch-keys https://raw.githubusercontent.com/ros/rosdistro/master/ros.asc
     sudo apt-add-repository http://packages.ros.org/ros2/ubuntu

#### Download ROS2 Foxy

Next install foxy:

     sudo apt install -y ros-foxy-ros-base
     sudo apt install -y python3-argcomplete
     sudo apt install -y python3-colcon-common-extensions
     sudo apt install -y python3-vcstool

#### Final ROS2 Configuration

Next some modifications are made to make ROS2 more permanent:

     source /opt/ros/foxy/setup.bash
     echo "source /opt/ros/foxy/setup.bash" >> ~/.bashrc

## Firmware Development

Firmware development is a big topic.
This document only gets you to the point where you can download and existing program
and execute it on your microcontroller board (i.e. the NUCLEO-F7676ZI).
The program is called `blinky` and it blinks the LED on the Nucleo board.
A trivial change is done to the main program and the returned back to is initial state.

The `STM32CubeIDE` (Integrated Development Environment) uses the concepts of workspace and project:

* Workspace:
  A workspace is a directory where the IDE stores miscellaneous files needed by the IDE.
  In particular, this is the place where the IDE keeps track of your projects.
  Your workspace directory is generally not keep under revision control.
  The workspace directory defaults to `~/STME32CubeIDE/workspace/workspace_1.X.Y/`.
  It is recommended that you use this default workspace location.

* Project:
  A project is a directory that is self contained piece of software that can be downloaded
  to a microcontroller.
  The project directory *can* be stored as a sub-directory in the workspace.
  However, for this project that is not recommended.
  Instead, projects are stored in a different location (the HR2 `git` Repository).
  None-the-less, the workspace can work with these projects in various different directories.
  Projects can easily be added and removed from a workspace.

The terms workspace and project are heavily used,
so it is useful to have an idea of what they are beforehand.

Now, please follow the following steps:

1. Start `stm32cubeide`:

   This starts everything rolling.
   `stm32cubeide` should be in your path.
   So, typing `stm32cubeide` in a console window should work.

2. Select a workspace directory:

   `STM32CubeIDE` really wants a workspace.
   So the first thing you will see is a pop-up is window entitled `Select a directory as workspace`.
   The default workspace directory is `/home/USER/STM32CubeIDE/workspace_1.X.Y`.

   You can check `[x] Use this as the default and do not ask again`
   if you do no want see this pop-up again.

   Please click on the `[Launch]` button.
   
3. Main Screen.

   The main screen that pops up is pretty spartan at first.
   It has:

   * Title Bar:
     The standard title is on top.
     The current workspace (not selected yet!) is typically displayed in the title bar.

   * Command Bar:
     There is the standard bar of text commands `File`, `Edit`, ... , `Help`.
   
   * Tab Window:
     There is a tab window has the `[Information Center]` tab showing.
     It humorous to note that this tab is rather non-informative at first.
     Additional tabs are forthcoming.

   * Vertical Icon Bar:
     There is a vertical bar on left that has some inscrutable icons in it.
     You can hover your mouse over the icons to get slightly more descriptive names.

4. Open Project Explorer:

   Find the `[Restore]` icon in the vertical icon bar and click on it.

   Now the `[Project Explorer]` tab should be open.
   
   Click on `[Import projects...]`   

5. Project Import:

   The `[Import]` pop-up shows up.
   It wants you to `Select an import wizard:`.
   Please click just to the left of `[General]`,
   and some additional options should show up.
   
   Select on `[Existing Projects into Workspace]` and click on the `[Next>]` button.
   
6. Import Projects:

   The `[Import Projects]` window pops up.

   Now you get to `(x) Select  root directory` and  click on the `[Browse...]` button.
   Using a file chooser, select the directory `$HR2_DIRECTORY/software`,
   where `$HR2_DIRECTORY` is the directory that contains the local copy of the HR2 `git` repository.

7. Import `blinky`:

   A list of predefined HR2 projects should show up.
   Please click `[Deselect All]` followed by checking off on the one named `[x] blinky`.
   When you click on the `[Finish]` button, this will import the `blinky` project to your workspace.
   You should now have one project in your workspace.

8. Find `main.c`:

   The project explorer should show a `blinky` in it.
   This is a tree explorer.
   Open `blinky1` => `Core` => `Src` until `main.c` is showing.
   Double click on `main.c` to open up the `main.c` file.

9. `main.c` Tab:

    The `main.c` tab should show up.
    Scroll through it until you see the `int main(void)` function (approximately line 70.)
    This is the first function called by the program.

    Scroll down until you find the `Infinite loop` (approximately line 100.)
    You should see 3 `HAL_GPIO_TogglePin()` function calls
    followed by a `HAL_Delay()`.
    
    Eventually, you will edit the `HAL_Delay()` function call, but that is a little further below.

10. Plug in Nucleo Board:

    Now is a good time to plug the Nucleo-767ZI board into your development computer
    using a USB cable with male USB mini connector on it.
    There are two female USB connectors on the Nucleo-767ZI board.
    There is one next to the large RJ45 connector
    and there is one on the opposite end that is for the ST-Link module.
    Plug into the ST-Link module.
    A big red LED on ST-Link module should light up when you plug into it.
    In addition much smaller green power LED on the "main" board will light up.
    The big red LED is actually a bi-color LED that can switch between read and green.
    It changes colors as various things go on.
    
11. Verify Nucleo Board Found:

     When you run `lssub` in a console window, you should see a line that contains
    `STMicroelectronics ST-LINK/V2.1` or something quite similar to it.
    This means that your development computer sees the ST-Link board and
    it should be ready to use.
    
    If not, you have problems and need to figure what went wrong.

12. Download and Run Blinky:

    Now you are going to run the `blinky` program.

    Everything happens pretty fast once you do the steps below.
    The following things happen one after another:

    1. The code is going to be compiled into an downloadable executable.

    2. `STM32CubeIDE` opens a connection to the Nucleo board.
       The ST-Link LED which is normally red, turns green.

    3. While program is being downloaded,
       the ST-Link LED flashes between red and green

    4. The program starts running
       and flashing its green, blue, and red LED's on the main Nucleo board.

    5. The ST-Link LED returns to red it indicate that it is no longer connected.

    There is an icon bar across the top.
    One of the icons looks like a green bug.
    The boring one to the right is the `[Run]` icon
    Without clicking, hover over the `[Run]` button, to see if it shows `[Run main.c]`

    To the right of the button is black pull hierarchical menu triangle.
    The menu item you need to select is two levels deep.
    Everything happens when you release the mouse button.
    Select the following:

       "[Run main.c]` => `[Run As]` => `[STM32/Cortex M C/C++ Application]`.

    Now watch the light show.
    If you missed it the first time around, you can do it again.
    Smile!!! You just ran `blinky`.
    
13. Change Blink Rate.

    Got back to the `[main.c]` tab and find the `HAL_Delay()` function at approximately line 100.
    Edit it from `1500` to `50`.
    The delay is in millseconds, so the LED's will flash much more quickly.

    Do the same process as the previous step, but `[Save and Launch]` pop up window will show up.
    Click on `[OK]` and the new program will download with the slower blinking LED's.

14. Change Blink Rate Back.
    
    Change the `50` back to `1500` and download again.

15. Exit `STM32CubeIDE`.

    Using the `[File]` menu in the upper left, select `[Exit]`.
    The `STM32CubeIDE` should shut down.
    You may also unplug your Nucleo-767ZI board.

That is it for now.

### Micro-ROS

The micro-ROS documentation is still a work in progress.
Reasonable starting points are:

* [micro-ROS Home Page](https://micro.ros.org/):
  This is the top level page.
  At the time of this writing, the page is totally mangeled unless it is viewed in full screen mode.
  When will web page designers ever learn?
  (Sorry, that is a rhetorical question.)

* [micro-ROS Tutorials](https://micro.ros.org//docs/tutorials/core/overview/):
  The tutorials and demos are a reasonable place to start.

As an overview, various flavors of ROS2 run on different computers.

* Development Computer:
  The development computer is an 64-bit x86 machine that runs stock ROS2.
  GUI intensive tools such as RViz, STM32CubeIDE, etc. can be run here.
  All of these tools are compiled to 64-bit x86 code.
  The [Development Computer ROS2 Install](#development-computer-ros2-install) is described above.

* Robot Computer:
  The Robot computer computer is 64-bit Arm Raspberry Pi 4.
  ROS is already compiled for these platforms.
  The [Robot Computer ROS2 Installation](#robot-computer-ros2-installation) is described above.
  Only non-GUI programs are installed on the robot computer.
  The key program that needs to be run on the robot computer is called the micro-ROS agent
  and it dedicated to talking to the robot microcontroller.

* Robot Microcontroller:
  The Robot microcontroller is a 32-b Arm Microcontroller (STM32F767ZI).
  It is currently a Nucleo-F767ZI.
  It has code that interfaces the to the robot sensors and actuators.
  It all has code to communicate with the micro-ROS agent that runs on the Robot computer.

The protocol that glues all of this together is called Data Distribution Service (DDS).
All three of the computers have implementations of the DDS protocol.
The one on the Robot microcontroller is a stripped down version of DDS to make it fit.

### Micro-ROS on Linux

The
[First micro-ROS application on Linux](https://micro.ros.org//docs/tutorials/core/first_application_linux/)
runs everything on your Development computer.
Typing the scripts in the code to follow the tutorial is a bit error prone,
so there is a shell script in the HR2 `bin` directory call `uros_linux_install.sh`.
This program takes one argument which is a directory to install everything into.
It is perfectly acceptable to specify a directory in the `/tmp` directory the first time.
This allows any problems to be easily deleted.

Feel free to read the shell script file as you read through the tutorial.
It might make your life a little easier.

The
[First micro-ROS application on an RTOS](https://micro.ros.org//docs/tutorials/core/first_application_rtos/)
builds the micro-ROS agent to run on either your development computer or on your robot computer.
It also build the micro-ROS firmware which is downloadable to the Robot Microcontroller.
As with the first tutorial,
there is anither script in the `bin` directory called `uros_nucleo_install.sh`
that will install the micro-ros code and build both the agent and the firmware.
The first time you run this script do it on your Development computer.
Eventually, you will rerun the same script on your Robot computer (i.e. the Raspberry Pi 4.)

<!--

Errors when running `.../bin/uros_nueclo_install /tmp/foo jnugen` on a Ras Pi 4,:

* `/tmp/foo/install/micro_ros_setup/config/freertos/list_apps.sh: line 25: pushd: /tmp/foo/firmware/freertos_apps/apps: No such file or directory`

* `/tmp/foo/install/micro_ros_setup/lib/micro_ros_setup/build_firmware.sh: line 65: /tmp/foo/firmware/dev_ws/install/setup.bash: No such file or directory`

* `/tmp/foo/install/micro_ros_setup/lib/micro_ros_setup/build_firmware.sh: line 65: /tmp/foo/firmware/dev_ws/install/setup.bash: No such file or directory`

* `=== ./uros/rclc (git) ===`
  `Could not checkout ref 'master': fatal: invalid reference: master`

-->

<!--

###################################################################################################

This is all old text that will eventually be deleted.

Developing firmware is done using `STM32CubeIDE`.
`STM` stands for `ST Microsystems` (where `ST` stands for `SGS-Thomson`).
It is unlear what `Cube` stands for, it was probably cooked up by the marketing department.
`IDE` stands for `Integrated Development Environment`.
The program is named `stm32cubeide` and should be in your execution path.

The Project directory has some additional structure that is discussed further below.

Note that the user interface people are constantly changing things around,
so these descriptions will get out of date fast.

Now it is time run `stm32cubeide`:

1. The first window that pops up is the `Select a directory as workspace` window.
   The default directory is as described above.
   You might want to check off the box labeled
   `[x] Use this as the default and do not ask again`.
   Finally click on the `[Launch]` button.

2. Next comes the `Welcome...` screen.

3. Click on `[File]` => 'New STM32 Project'.

4. Next pops up the `Target Selection Window`.

5. There are 4 tabs -- `[MCU/MPU Selector]`, `[Board Selector]`, and two others.
   The first tab is used to select raw chips 

   Click on `[Board Selector]`.

6. In the `Commercial Part Number` entry field, type `767`.
   This will constrain the search to board to boards that contain `767`.

7. Click on `[NUCLEO-F767ZI]` followed by `[Next]`.

8. The `STM32 Project` window comes up.
   The options should default to `C`, `Executable`, and `STM32Cube`.

9. Type your project name `blinky` into the `Project Name:` field.

10. In a console window, type `mkdir /tmp/blinky`,
    to create a temporary directory to experiment with a blinking diode application.

11. Back in the `STM32 Project` window,
    unclick `[x] Use default location`, and
    type in `/tmp/blinky` into to the `Location:` entry field.

12. Now click on `[Finish]`.

13. A window pops up with `Initialize all peripherals with their default Mode ?`.
    Click on `[Yes]`.

14. Next a
    `Device Configuration Tool editor is associated with Device Configuration Toolperspective.`
    `Do you want to open this perspective now?` pop-up occurs.
    Click on `[Yes]`.

15. At this point a huge amount of additional files get downloaded and unzipped.
    Thankfully, these files rarely need to be downloaded again.

16. At this point in time, the `/tmp/blinky/` directory has been populated
    a bunch of files and sub-directories.

17. On the left is the `[Project Explorer]` tab which shows all of the files
    that have been populated into `/tmp/blinky/`.
    At the top level are the `Includes/`, `Core/`, and `Drivers/` directories.
    Generally speaking `Core/` sub-directory contains source code that can be edited by you,
    whereas the `Includes/` and `Drivers/` sub-directories contains the header files
    that should not be edited by you.
    In addition, the `blinky.ioc` file is generated,
    which specifies all of the pin bindings for the microcontroller.
    All `.ioc` files are managed by the `stm32cubeide`.
   
18. The `[blinky.ioc]` tab contains a tabbed panel with 4 sub-panels.

    These are:
    * `[Pinout & Configuration]`:
      This contains a picture of the `STM32F767ZI` microcontroller.
    * `[Clock Configuration]`:
      This contains an amazingly complex timing chart.
    * `[Project Manager]`:
      This is panel that is similar to `[Project Window]` used to originally create the project.
      It has some additional side tabs and features that can be ignored for now.
    * `[Tools]`:
      This is some advanced tools for power management.
    
19. In the `[Pinout & COnfiguration]' tab, the Ethernet peripheral needs to be disabled.
    This id done by clicking `[Connectivity]` => `[Eth]`.
    Next, in `ETH Mode and Configuration` there is a `Mode` scrollable drop down menu
    that shows `[RMII]`.
    Select the drop down menu and scroll upward to `[Disable]`.

20. In the top icon bar, click on the hammer to build the `[Debug]` configuration.

21. Now is a good time to plug the Nucleo-767ZI board into your development computer
    using a USB cable with male USB mini connector on it.
    There are two female USB connectors on the Nucleo-767ZI board.
    There is one next to the large RJ45 connector
    and there is one on the opposite end that is for the ST-Link module.
    Plug into the ST-Link module.
    A big red LED on ST-Link module should light up when you plug into it.
    In addition much smaller green power LED on the "main" board will light up.
    The big red LED will flash back and for between red and green when the 
    
22. When you run `lssub` in a console window, you should see a line that contains
    `STMicroelectronics ST-LINK/V2.1` or something quite similar to it.
    This means that your development computer sees the ST-Link board and
    it should be ready to use.
    
23. Now it is time to download and the null program into the microcontroller and "debug it".
    Up in the icon bar at the top, there is a bug with six legs.
    This is the debugger icon and to the right of this icon is a pull down menu.
    Click on the pull down menu and it will give some options.
    `STM32/Cortex M C/C++ Application`.
    It may put up a `[Choose launch configuration to debug]` window.
    Please select on `[blinky Debug]` and click `[OK]`.
    If you look quickly you will see the ST-link LED flashing between Red and Green.
    
24. Frequently, a `[Confirm Perspective Switch]` pop-up will appear.
    Please click on `[Switch]`.
    This window comes up a lot, so you make decide to click on `[x] Remember my decision`.

25. Next to this icon is a drop down menu with downward pointing triangle.
    Click on this triangle to get the drop down menu.
    
26. The `[main.c]` table should be selected and a line labeld `HAL_Init();` should be highlighted.
    To the left of this should be a little blue arrow that indicates where
    the program is currently paused.

27. There are a number of debugger icons that showed up.
    There is an icon Red square with green triangle underneath.
    This the `[Terminate and Relaunch]` button.
    If you hover over this button, hover help shows up.
    Move to there right to hover help for each debugger icons.
    The three most important ones are the single stepping icons which are yellow arrows.
    (One my be grayed out.)

29. Click on the `[Terminate]` icon (big red square).
    This causes the ST-Link to disconnect and show the LED Red rather than flashing Red/Green.

30. Now this temporary project can be deleted by going to the `[Project Explorer]` tab.
    Right click on the `[blinky]` project, and select `[X Delete]`, and click on `[OK]`.
    Now the temporary project is gone from the workspace.

More Notes:

* The code seems to stash files all over the place:
  * `~/STM32Cube/`: All of the files land here.
  * `~/STM32CubeIDE/`:
  * `~/STM32CubeIDE/workspace/`:
  * `~/STM32CubeIDE/workspace/workspace_1.5.0/`:
  * `~/STM32CubeIDE/workspace/workspace_1.5.0/.metadata/`:  This 
  * `~/stm32cubeide/`:
  * `~/stm32cubemx/`:
  * `~/stm32cube/`:
  * `~/stm32cufinder/`:

Notes:

People started stuff should start with `stm32cubeide` from STM(STMicroelectronics.)

[STM32CubeIDE ST-LINK GDB server](https://www.st.com/resource/en/user_manual/dm00613038-stm32cubeide-st-link-gdb-server-stmicroelectronics.pdf)

[Another link to previous solution](https://stackoverflow.com/questions/57312510/debug-remotely-on-stm32cubeide-with-an-stm32-eval-board)

[Where to find stlink-gdb-server](https://community.st.com/s/question/0D50X0000BmnDcXSQU/question-on-stm32cubeide-and-remote-debugging)
They do not have a Linux version of this software.

[F5/F6 key Config](https://hbfsrobotics.com/blog/configuring-vs-code-arm-development-stm32cubemx)

## Roadmap

The steps required to do this are:

1. Blinky:
   Install enough code on the host computer to be able compile and download
   a blinkng LED program (i.e. blinky) onto an STM Nucleo board.
   Debugging is not supported yet.

2. Codium:
   Download `vscodium` (the community maintained version of `vscode`.)
   Configure it to support download *and* debug.

3. Host Computer ROS2 Install:
   Install ROS2 on a Ubuntu 20.04 host machine.

4. Robot Computer ROS2 Install:
   Bring up Ubuntu on the Robot computer, bring up WiFi connectivity, and download ROS2.

5. MicroROS:
   Bring up MicroROS on the Nucleo board and get it to talk to the Raspberry Pi 4.

## Current Status: Working through Embedded Geek Videos:

I'm currently about half way through the first video:
1. [Command line](https://www.youtube.com/watch?v=PxQw5_7yI8Q)

     openocd -f interface/stlink-v2-1.cfg -f target/stm32f7x.cfg -c "program $(BUILD_DIR)/$(TARGET).elf verify reset exit"

2. [VSCode](https://www.youtube.com/watch?v=xaC5oWwzOt0)

## Blinky

The blinky task is to download a trivial blinking LED program into Robot microcontroller.
This ensures that the necessary tools (i.e. the tool chain) is present
and a reasonable workflow is present.

Two paths strategies were ultimately considered:

* `stm32cubeide`:
  `stm32cubeide` is a version of the Eclipse IDE (Integrated Development Environment)
  that has been configured for STM microcontroller software development.
  In particular, is integrated with a piece of code that STM calls `stm32cubemx`.
  `stm32cubemx` is program for configuring the various peripherals inside of an STM microcontroller.

* `vscode`:
  `vscode` is an IDE (Integrated Development Environment) that is developed and maintained
  primarily by Microsoft.
  It is primarily written in C# and is released under a the MIT license.
  Importantly, it seems to be possible to configure it to work well with `git`.

In the end, the `vscode` path won out over the `stm32cubeide`.
The reason was subtle and had to do issues of getting `stm32cubeide` to work well with `git`.
`stm32cubeide` likes to embed the full paths to files in its configuration files
where as `vscode` does not.
Various workarounds were found on the net, but they were all pretty ugly.
The `vscode` option is viable is because the critical piece of software is `stmcubemx` is
available as a standalone program.

The road map for blinky is:

1. Install Common Tools.
   The common tools need to be installed.

2. Install `STM32CubeMX`:
   The `stm32cubemx` program needs to be installed.

3. Install ARM Cross Compilers:
   ARM cross compiliers need to be installed.

4. Create an `STM32CubeMX` Project:

### Install Common Tools

The common tools are installed via `sudo apt install --yes` which downloads the
necessary packages from the Ubuntu main package repository:

     sudo apt install --yes build-essential git  # Needed for make, git, etc.
     sudo apt install --yes openocd  # Needed for download/debug
     sudo apt install --yes openjdk-8-jdk  # Needed for `stm32cubemx`
     sudo apt install --yes libncurses5 libncurses5:i386  # Needed for ARM `gdb` debugger

### Install STM32CubeMX

The STM32CubeMX is program developed by ST that is used to configure various ST microcontrollers.
ST has developed a HAL (Hardware Abstraction Library) that is shared across the entire product line.
The STM32CubeMX program generates code that makes calls to the HAL.
It very much worth the annoyance and tedium of downloading and installing this program.

The STM32CubeMX is not open source software.
STM32CubeMX appears to be written in Java and needs to run under the JRE (Java Runtime Environment).
In a step above, the JRE is installed.

In order to run this software the following steps need to occur:

1. Download.
   Download and install the STM32CubeMX.

3. Wrapper.
   Create a wrapper that calls STM3CubeMX.

The download and install process is pretty involved and is frankly pretty annoying.

#### Download the STM32CubeMX:

Downloading the STM32CubeMX is pretty involved.

The [STM32CubeMX Web Page](https://www.st.com/en/development-tools/stm32cubemx.html)
is a good place to start.
Note, whenever ST decides to reorganize their web site, the link above will probably fail.

Basically, you must create an account with ST before you can get the software.
Just click on the [Get Software] button on the web mentioned immediately above to start the process.
Fill in the forms and wait for the account to happen.
(In the past, it took a while, but perhaps account setup is bit faster now.)
ST will offer the you the wonderful opportunity to let them send you lots of marketing information,
but they also give you the opportunity to decline this generous offer.

You need to be logged into you ST account before they will graciously allow you
to download the wonderful STM32CubeMX install and setup program.
Eventually, you will get your hands of a file named something like:

     SetupSTM32CubeMX-6.1.1.linux

The version number will change over time.
This is an executable 64-bit x86-64 executable file.
When you execute this file (i.e. `./SetupSTM32CubeMX-6.1.1.linux`),
it will make you accept their license agreement again (you can never be too sure):

* [X] I accept the terms of this license agreement.
* [X] I have read and understood the ST Privacy and ST Terms of Use
* [ ] I consent that ST in N.V. ...   (no need to click this one!)
* Install directory:  Pick someplace like `.../stm32cubemx/stm32cubemx-6.1.1`.
  Make sure the directory does not previously exist.
* [OK]  The target directory will be created.
* [X] Auto installer (seems harmless)

Obviously, the sequence of questions will change over time at the discretion of ST.
The final executable is should show up as something like
`.../stm32cubemx/stm32cubemx-6.1.1/STM32CubeMX`.

#### `stm32cubemx` Wrapper

Due to the fact that the code is ultimately running the byte codes in the JRE,
it is best to provide a wrapper that executes the program.
The primary reason for wrapper is to make sure that JRE can find the byte codes.
The safest way to ensure that it always finds the byte codes is to always execute the program
with a full execution path specified (i.e. `/.../STM32CubeMX`.)

The final executable tends spews out a great deal of text to the console.
This first time you run the executable,
you can see what sort of exciting information is being spewed to the console.
After that you may choose run it with `> /dev/null` tacked onto the end
in order to send the intensely exciting console information to the bit bucket.

Add the following to your `.bashrc` file (or equivalent):

     export STM32CUBEMX_BIN_DIR="$HOME/download/stm32cubemx/stm32cubemx-6.1.1"
     export PATH=":$STM32CUBEMX_BIN_DIR:$PATH:"

Now in the same directory that contains `STM32CubeMX`,
create a file called `stm32cubemx` (lower case) with the following content:

     #!/usr/bin/env bash
     # STM32CUBEMX_BIN_DIR must be defined in `$HOME/.bashrc`:
     $STM32CUBEMX_BIN_DIR/STM32CubeMX "$@" > /dev/null

Remember the `> /dev/null` on the last line is optional,
but most people will prefer to leave it in there.

In order to test the `.bashrc` modifications, do the following:

     source ~/.basrhc
     stm32cubemx

The `stm32cubemx` should cause the initial window of the `STM32CubeMX` program to pop up.
The first time the program is started, it will ask additional questions.
It really wants to collect information about your usage, but you can say "No thanks".

Ultimately, the STM32CubeMX program is used to create and manage an `.ioc` file.
Presumably, `.ioc` stands for I/O Configuration, but it could *stand* for something else.
In addition to managing the `.ioc` file, it also generates configuration code for the HAL library.

### Install ARM Cross compilers

Every quarter,
Arm Holdings releases a bunch of Arm cross-compilers that run on the x86 architecture,
but generate code for the Arm architecture.
The (ARM cross compilers web page)[https://developer.arm.com/tools-and-software/open-source-software/developer-tools/gnu-toolchain/gnu-rm/downloads],
provides links to the appropriate downloads.
The one of interest is `gcc-arm-none-eabi-...x86_64-linux.tar.bz2`,
where `...` specifies the `VV-YYYY-qQ` (VV=10+, YYYY=202x, Q=1-4).

Store this file into a directory like `.../gcc-arm-none-eabi`.
Unpack using the following commands:

     bunzip2 *.bz2
     tar xvf *.tar

This should result in a sub-directory that looks something like
`gcc-arm-none-eabi-10-2020-q4-major`.

Edit your `~.bashrc` (or equivalent) to do add the followings:
    
     # Fill in `...` as appropriate:
     export GCC_ARM_BIN=".../gcc-arm-none-eabi/gcc-arm-none-eabi-10-2020-q4-major/bin"

Be sure to make it match the actual version that was downloaded, since they are updated quarterly.

###  Create an `STM32CubeMX` Project:

If everything has gone right, the following programs should be in your path:

     gcc-arm-none-eabi-gdb --version
     openocd --version
     codium --version
     stm32cubemx  

## Construct an STM32CubeMX project.

The STM32CubeMX program organizes things into a WORKSPACE directory and
associated PROJECT directories.
For these examples, the WORKSPACE directory is `$HR2_DIRECTORY/software/non_ide/`.
The blinky PROJECT directory is `$HR2_DIRECTORY/software/non_ide/f767zi_blinky`.

The WORKSPACE directory is created manually using:

     mkdir -p $HR2_DIRECTORY/software/non_ide/f767z

Now run `stm33cubemx`:

    `stm32cubemx`

1. Under the `New Project` heading, find `Start My project from ST Board`.
   (It may necessary to expand `stm32cubmx` full screen in order to see this text in its entirety.)
   Click on the `[Access To Board Selector]` button.
   A window shows up with multiple tabs.
   The selected tab should be `[Board Selector]`.
  
2. (Optional) There is a text entry box called `Commercial Part Number`
   into which you may type a partial part number.
   For example, if you type `767` in this constrain all parts to contain `767`.

3. Select the `MCU/MPU Series`.
   For the `767` part, this is the `[x] STM32F7`.

4. There will be a `Boards List` that lists the boards that match.
   In this case, we want `Nucleo-F767ZI`, so please click on it.

5. Next, click on `[ ]--> Start Project`

6. A Popup that says `? Initialize all peripherals with their default Mode? [Yes] [No]`
   shows up.  Click on `[Yes]`.

7. A window with 4 tabs shows up.
   The 4 tabs are:

   * `[Pinout & Configuration]`:
      This one shows the outline of the integrated circuit with various pins highlighted.
      This is the initially selected tab.
      For now, we ignore this tab.

   * `[Clock Configuration]`:
      This one shows the clock configuration diagram, which can be quite complicated.
      For now, leave this one alone.

   * `[Project Manager]`:
      This one is used for setting up the project.
      There are numerous things on this tab.
      In the next step below, this tab is used.

   * `[Tools]`:
         This is some advanced tools that are ignored for now.

8. Select the `[Project Manager]` tab and fill in the following fields:

   * `Project Name`:
      Give the project a name.
      It is recommended that the name include at some fraction of the processor.
      For example, `blinky_f767zi`.

      * `Project Location`:
         This the WORKSPACE directory.
	 You must either browse or manually type in the full path to this directory.
        
      * `Toolchain / IDE`:
         This is a selection box that is normally set to `[EWARM]`.
         It is very important to change this to `[Makefile]`

 9. Select the `[Pinout & Configuration]` tab:

    * Select the `Connectivity >` drop down menu and select `ETH`.

    * A `Mode` side window shows up.
      It probably is showing a `Mode` of `RMII`.
      Scroll up to the first entry of the drop down menu and select `Disable`.
      This will disable the intialization of the Ethernet device.
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

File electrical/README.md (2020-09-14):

<!--
MIT License

Copyright 2020 Home Brew Robotics Club

Permission is hereby granted, free of charge, to any person obtaining a copy of this
software and associated documentation files (the "Software"), to deal in the Software
without restriction, including without limitation the rights to use, copy, modify,
merge, publish, distribute, sublicense, and/or sell copies of the Software, and to
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

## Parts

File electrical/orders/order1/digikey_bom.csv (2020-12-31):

Qty | Digi-Key PN | Description | Customer Note | Price | Ext. Price | Mfg. | Mfg. PN | Ref. Designator
5 | A108891CT-ND | BATTERY HOLDER COIN 6.8MM SMD | COIN_HOLDER6.8R;TE1376164-1 | $3.35 | $16.75 | TE Connectivity | 1376164-1 | mBT1
10 | 493-1304-ND | CAP ALUM 470UF 20% 25V RADIAL | 470µF,25Vmin;D10P5H13max | $0.31 | $3.06 | Nichicon | UVZ1E471MPD | mC4,mC2
5 | 493-15115-ND | CAP ALUM 1000UF 20% 10V RADIAL | 1000µF@10Vmin;D10P5H13max | $0.42 | $2.10 | Nichicon | UFW1A102MPD | mC3
10 | 670-2950-1-ND | CONN RCPT USB3.1 TYPEC 24POS SMD [USB-C]] | USB-C | $0.67 | $6.71 | JAE | DX07S024WJ3R400 | mCN1,mCN2
40 | S7037-ND | CONN HDR 4POS 0.1 GOLD PCB [F1x4] | F1x4 | $0.44 | $17.48 | Sullins | PPPC041LFBN-RC | mCN21,mCN3,mCN19,mCN10,mCN9,sCN2,mCN11
5 | S7038-ND | CONN HDR 5POS 0.1 GOLD PCB [F1x5] | F1x5 | $0.49 | $2.45 | Sullins | PPPC051LFBN-RC | mCN3
10 | S1011EC-40-ND | CONN HEADER VERT 40POS 2.54MM [M1x40] | M1x2/3/4 | $0.58 | $5.82 | Sullins | S1011EC-40-ND | mCN17,mJP10,lCN1,mCN24,mJP9,mCN13,mCN25,mCN28,mCN15,mJP7,mCN29,mJP5,mCN23,mJP3,mJP2,mCN26,mCN18,mCN27,mCN4,mJP8,mJP6,mCN22,mJP1,mJP4
5 | S9200-ND | CONN HDR 40POS 0.1 GOLD PCB [F2x20] | F2x20 | $1.94 | $9.70 | Sullins | SFH11-PBPC-D20-ST-BK | mCN5
25 | S7036-ND | CONN HDR 3POS 0.1 GOLD PCB [F1x3] | F1x3 | $0.35 | $8.77 | Sullins | PPPC031LFBN-RC | mCN6,mCN7,mCN21
5 | S7072-ND | CONN HDR 8POS 0.1 TIN PCB [F2x4] | F2x4 | $0.67 | $3.35 | Sullins | PPTC042LFBN-RC | mCN8
2 | 1212-1125-ND | CONN SOCKET 64POS 0.1 GOLD PCB [HCS404LP;F1x4] | HCSR04LP;F1X4LP | $3.85 | $7.70 | Preci-Dip | 315-87-164-41-003101 | mCN12,mCN14,mCN16
10 | S2211EC-40-ND | CONN HEADER VERT 80POS 2.54MM [M2x40] | F2x40 | $1.91 | $19.11 | Sullins | PRPC040DFAN-RC | mCN20
5 | 2057-BHR-12-VUA-ND | CONN HEADER VERT 12POS 2.54MM [M2x6S] | WOW_OUT;M2x6S | $0.31 | $1.55 | Adam Tech | BHR-12-VUA | mCN30
100 | TLPG5600-ND | LED GREEN DIFF SIDE LED T/H R/A | LED;GRNRA | $0.19 | $19.39 | Vishay | TLPG5600 | mD7,mD12,mD6,mD18,mD13,mD17,mD21,mD19,mD10,mD8,mD15,mD9,mD20,mD14,mD11,mD16
10 | 1727-6963-1-ND | IC GATE AND 1CH 3-INP 6TSOP | 74x11G1;TSOP6 | $0.29 | $2.86 | Nexperia | 74LVC1G11GV,125 | mU17,mU16
10 | MCP2542FDT-E/SNCT-ND | IC TRANSCEIVER 1/1 8SOIC | MCP2542;SOIC8 | $0.77 | $7.70 | Microchip | MCP2542FDT-E/SN | mU18,mU19
5 | 1727-5983-1-ND | IC FF D-TYPE SNGL 1BIT 8TSSOP | 74LVC1G74;TSSOP8 | $0.39 | $1.95 | Nexperia | 74LVC1G74DP,125 | mU20
2 | S1111EC-40-ND | CONN HEADER R/A 40POS 2.54MM [M1x40RA] | M1x?RA | $0.74 | $1.48 | Sullins | PRPC040SBAN-M71RC | eCN1
20 | AH1806-W-7DICT-ND | MAGNETIC SWITCH OMNIPOLAR SC59 | AH1806;SC59 | $0.37 | $7.40 | Diodes Inc. | AH1806-W-7 | eQ1,eQ2
30 | 541-3966-1-ND | RES 47K OHM 1% 1/16W 0402 | 47KΩ;1005 | $0.03 | $0.87 | Vishay | CRCW040247K0FKEDC | eR1,MISC6,eR2
1 | S2112EC-40-ND | CONN HEADER R/A 80POS 2.54MM [M2X80RA] | M2x?RA | $1.59 | $1.59 | Sullins | PREC040DBAN-M71RC | sCN1
20 | S7000-ND | CONN HDR 2POS 0.1 GOLD PCB [F1x2] | F1x2 | $0.31 | $6.12 | Sullins | PPPC021LFBN-RC | sCN2
5 | S7039-ND | CONN HDR 6POS 0.1 GOLD PCB [F1x6] | F1x6 | $0.53 | $2.65 | Sullins | PPPC051LFBN-RC | sCN2
5 | 455-1659-ND | CONN HEADER VERT 4POS 1.5MM [LD06_CONN;M1x4P1.5ZH] | LD06_CONN;M1x4P1.5ZH | $0.22 | $1.10 | JST | 455-1659-ND | lCN2
2 | 1690-RASPBERRYPI4B/4GB-ND | RASPBERRY PI 4 MODEL B 4GB SDRAM | RASPI4 | $55.00 | $110.00 | RasPi | RPI4-MODBP-4GB | MISC1
5 | 1597-110991327-ND | HEAT SINK KIT FOR RASPBERRY PI 4 | RP4_HEAT_SINKS | $0.99 | $4.95 | SeeedStudio | 110991327 | MISC2
1 | 497-16525-ND | NUCLEO-144 STM32F767 DEV EVAL BD | NUCLEO_767ZI | $24.47 | $24.47 | STM | NUCLEO-F767ZI | MISC3
60 | 455-1281-1-ND | CONN SOCKET 28-32AWG CRIMP TIN | ZH_CRIMP_PIN | $0.02 | $1.31 | JST | SZH-003T-P0.5 | MISC4
12 | 455-1202-ND | CONN HOUSING ZH 4POS 1.5MM WHT | ZH_HOUSING | $0.09 | $1.02 | JST | ZHR-4 | MISC5
3 | 1690-1011-ND | RASPBERRY PI CAMERA MODULE V2 | RPI_CAM_V2 | $25.00 | $75.00 | RasPi | 913-2664 | MISC7
10 | 2057-FCS-12-SG-ND | SOCKET FLAT CABLE IDC 12P 2.54MM | F2x6;IDC | $0.44 | $4.40 | Adam | FCS-12-SG | MISC8

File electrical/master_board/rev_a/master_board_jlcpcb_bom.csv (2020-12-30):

Comment | Designator | Footprint | LCSC Part #
Ta22uF6.3V;3216 | C1, | CASE-A | C135574
2.2uF6.3V;1608 | C10, | 0603 | C23630
0.01uF;1005 | C16, | 0402 | C15195
15pF;1608 | C5, C7, | 0603 | C1644
0.1uF;1005 | C6, C8, C11, C12, C13, C14, C15, C17, C18, C19, C20, C21, C22, C23, | 0402 | C1525
10uF;1608 | C9, | 0603 | C19702
LEDGRN;1608 | D1, D2, D3, D4, D5, | LED_0603 | C72043
REDLED;1608 | D22, | LED_0603 | C2286
NFET_3A_GSD;SOT23 | Q1, Q2, Q3, | SOT-23-3L | C20917
2N7002;SOT23 | Q4, Q6, Q7, Q8, Q9, Q10, Q11, Q12, Q13, Q14, Q15, Q16, Q17, Q18, Q19, Q20, Q21, Q22, Q23, Q25, | SOT-23-3 | C8545
PFET_6A_GSD;SOT23 | Q5, Q24, | SOT-23-3 | C141546
10KOhm;1005 | R1, R2, R3, R4, | 0402 | C25744
100KOhm;1608 | R13, | 0603 | C25803
100KOhm;1005 | R14, R15, R16, R18, R19, R21, R22, R23, R24, R43, R47, R48, R49, R50, R51, R52, R53, R54, R55, | 0402 | C25741
1KOhm;1005 | R17, R44, | 0402 | C11702
.16Ohm.25W;2012 | R25, R26, | 0805 | C34388
270Ohm;1608 | R27, R28, R29, R30, R31, R32, R33, R34, R35, R36, R37, R38, R39, R40, R41, R42, | 0603 | C22966
2.2KOhm;1005 | R45, | 0402 | C25879
3.3KOhm;1005 | R46, | 0402 | C25890
33Ohm;1005 | R5, R20, | 0402 | C25105
120Ohm;1005 | R57, | 0402 | C25079
120Ohm.25W;3216 | R58, R59, | 1206 | C17909
220Ohm;1005 | R6, R8, | 0402 | C25091
300Ohm;1608 | R60, R61, | 0603 | C23025
560Ohm;1608 | R7, | 0603 | C23204
0Ohm;3216 | R9, R10, R11, R12, R56, | 1206 | C17888
BUTTON;6x6 | SW1, SW2, | SMD-4 | C127509
LM5050-1;TSOT-23-6 | U1, U2, U3, | SOT-23-6L | C55266
CD4504B;TTSOP16 | U10, U11, | TSSOP-16 | C233582
ACS711;SOIC8 | U12, | SOIC-8 | C10681
SN74HC165;TSSOP16 | U14, U15, | HTSSOP-16 | C201716
CPC1017N;SOP4W3.8L4.1 | U21, U22, | SOP-4 | C261926
MCP7940;SOIC8 | U4, | SOIC-8 | C7440
CAT24C32;SOIC8 | U5, | SOIC-8 | C81193
DRV8833PWPR;HTSSOP16EP3.4x5 | U6, | HTSSOP-16 | C50506
SN74HC595;TSSOP16 | U7, U8, U9, U13, | HTSSOP-16 | C5948
AMS1117-3.3V800mA_GOI;SOT223 | VR1, | SOT-223 | C6186
32.768kHz12.5pF;3.2x1.5 | X1, | SMD-3215 | C32346

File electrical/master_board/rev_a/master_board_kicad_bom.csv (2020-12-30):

Source: | /home/wayne/public_html/projects/hbrc_ros_robot_platform/electrical/master_board/rev_a/master_board.sch
Date: | Tue 29 Dec 2020 04:47:55 PM PST
Tool: | Eeschema 5.1.9-73d0e3b20d~88~ubuntu20.04.1
Generator: | /usr/share/kicad/plugins/bom_csv_grouped_by_value_with_fp.py
Component Count: | 226
Ref | Qnty | Value | Cmp name | Footprint | Description | Vendor
BT1, | 1 | COIN_HOLDER6.8R;TE1376164-1 | Battery_Cell | HR2:TE1376164-1_COINHOLDER6.8 | Single-cell battery
C1, | 1 | Ta22µF6.3V;3216 | C | Capacitor_SMD:C_1206_3216Metric | Unpolarized capacitor
C2, C4, | 2 | 470µF,25Vmin;D10P5H13max | CP1 | Capacitor_THT:CP_Radial_D10.0mm_P5.00mm | Polarized capacitor, US symbol
C3, | 1 | 1000µF@10Vmin;D10P5H13max | CP1 | Capacitor_THT:CP_Radial_D10.0mm_P5.00mm | Polarized capacitor, US symbol
C5, C7, | 2 | 15pF;1608 | C | Capacitor_SMD:C_0603_1608Metric | Unpolarized capacitor
C6, C8, C11, C12, C13, C14, C15, C17, C18, C19, C20, C21, C22, C23, | 14 | 0.1µF;1005 | C | Capacitor_SMD:C_0402_1005Metric | Unpolarized capacitor
C9, | 1 | 10µF;1608 | C | Capacitor_SMD:C_0603_1608Metric | Unpolarized capacitor
C10, | 1 | 2.2µF6.3V;1608 | C | Capacitor_SMD:C_0603_1608Metric | Unpolarized capacitor
C16, | 1 | 0.01µF;1005 | C | Capacitor_SMD:C_0402_1005Metric | Unpolarized capacitor
CN1, | 1 | USB-C;USB-C,POGND | USB-C;USB-C,POGND | Connector_USB:USB_C_Receptacle_JAE_DX07S024WJ3R400
CN2, | 1 | USB-C;USB-C | USB-C;USB-C | Connector_USB:USB_C_Receptacle_JAE_DX07S024WJ3R400 | USB-C Connector
CN3, | 1 | POLOLU_U3V70F9;F1x4+F1x5 | U3V70xMATE;F1x4+F1x5 | HR2:U3V70xMATE_F1x4+F1x5 | Pololu U3V70x Voltage Regulator Mating Connector
CN4, | 1 | RPI_DSP_PWR;M1x2 | Conn_01x02 | Connector_PinHeader_2.54mm:PinHeader_1x02_P2.54mm_Vertical | Generic connector, single row, 01x02, script generated (kicad-library-utils/schlib/autogen/connector/)
CN5, | 1 | RASPI;F2X20 | RASPI;F2X20 | HR2:RASPI_F2X20
CN6, CN7, | 2 | HR2_ENCODER;2xF1x3 | ENCODER;2xF1x3 | HR2:ENCODER_2xF1x3 | HR2 Encoder Connector
CN8, | 1 | STADAPTER;F2x4 | STADAPTER;F2x4 | HR2:STADAPTER_F2x4 | ST Adapter Mating Connector
CN9, CN10, | 2 | HCSR04H;F1X4H | HCSR04H;F1X4 | HR2:HCSR04_F1x4H | HC-SR04 Sonar (High Profile Receptacle)
CN11, CN19, | 2 | HCSR04;F1X4 | HCSR04;F1X4 | HR2:HCSR04_F1x4 | HC-SR04 Sonar (Normal Profile Receptacle)
CN12, CN14, CN16, | 3 | HCSR04LP;F1X4LP | HCSR04LP;F1X4 | HR2:HCSR04_F1x4LP | HC-SR04 Sonar (Low Profile Receptacle)
CN13, CN15, CN17, | 3 | SERVO;M1x3 | SERVO;M1x3 | Connector_PinHeader_2.54mm:PinHeader_1x03_P2.54mm_Vertical | Servo F1X3
CN18, | 1 | SERVO;M1x4 | SERVO;M1x4 | Connector_PinHeader_2.54mm:PinHeader_1x04_P2.54mm_Vertical | Servo M1X4
CN20, | 1 | NUCLEO-F767ZI;2xF2x35 | NUCLEO-F767ZI;2xF2x35 | HR2:NUCLEO_F767ZI_2xF2x35 | NUCLEO144-F767ZI
CN21, | 1 | LIDAR_ADAPTER;2xF1x4_F1x3 | LIDAR_ADAPTER;2xF1x4_F1x3 | HR2:LIDAR_ADAPTER_2xF1x4_F1x3 | Lidar Adapter Connectors
CN22, CN23, CN24, CN25, CN26, CN27, CN28, CN29, | 8 | SENSE;M1x3 | SENSE;M1x3 | Connector_PinHeader_2.54mm:PinHeader_1x03_P2.54mm_Vertical | Sense F1X3
CN30, | 1 | WOW_OUT;M2x6S | WOW_OUT;M2x6S | HR2:PinHeader_2x06_P2.54mm_Vertical_Shrouded
D1, D2, D3, D4, D5, | 5 | LEDGRN;1608 | LED | LED_SMD:LED_0603_1608Metric | Light emitting diode
D6, D7, D8, D9, D10, D11, D12, D13, D14, D15, D16, D17, D18, D19, D20, D21, | 16 | LED;GRNRA | LED | HR2:LED_GRNRA | Light emitting diode
D22, | 1 | REDLED;1608 | LED | LED_SMD:LED_0603_1608Metric | Light emitting diode
GV1, GV2, GV3, GV4, GV5, | 5 | GROVE;20x20 | GROVE;20x20 | HR2:GROVE20x20 | Grove 20x20 Module
H1, H2, H3, H4, H5, H6, | 6 | HOLE;M2.5 | HOLE;M2.5 | MountingHole:MountingHole_2.7mm_M2.5
JP1, JP8, | 2 | LED_EN;M1x3 | Jumper_3_Open | Connector_PinHeader_2.54mm:PinHeader_1x03_P2.54mm_Vertical | Jumper, 3-pole, both open
JP2, JP3, JP4, JP5, JP10, | 5 | SHUNT;M1x2 | Jumper_2_Open | Connector_PinHeader_2.54mm:PinHeader_1x02_P2.54mm_Vertical | Jumper, 2-pole, open
JP6, | 1 | RPI_DISP_EN;M1x3 | Jumper_3_Open | Connector_PinHeader_2.54mm:PinHeader_1x03_P2.54mm_Vertical | Jumper, 3-pole, both open
JP7, | 1 | JUMPER;M1x2 | Jumper_NO_Small | Connector_PinHeader_2.54mm:PinHeader_1x02_P2.54mm_Vertical | Jumper, normally open, small symbol
JP9, | 1 | EXT_ESTOP;M1x2 | Jumper_2_Open | Connector_PinHeader_2.54mm:PinHeader_1x02_P2.54mm_Vertical | Jumper, 2-pole, open
Q1, Q2, Q3, | 3 | NFET_3A_GSD;SOT23 | Q_PWR_NMOS_GSD | Package_TO_SOT_SMD:SOT-23 | N-MOSFET transistor, drain/source/gate
Q4, Q6, Q7, Q8, Q9, Q10, Q11, Q12, Q13, Q14, Q15, Q16, Q17, Q18, Q19, Q20, Q21, Q22, Q23, Q25, | 20 | 2N7002;SOT23 | 2N7002 | Package_TO_SOT_SMD:SOT-23 | 0.115A Id, 60V Vds, N-Channel MOSFET, SOT-23
Q5, Q24, | 2 | PFET_6A_GSD;SOT23 | Q_PWR_PMOS_GSD | Package_TO_SOT_SMD:SOT-23 | P-MOSFET transistor, gate/source/drain
R1, R2, R3, R4, | 4 | 10KΩ;1005 | R_US | Resistor_SMD:R_0402_1005Metric | Resistor, US symbol
R5, R20, | 2 | 33Ω;1005 | R_US | Resistor_SMD:R_0402_1005Metric | Resistor, US symbol
R6, R8, | 2 | 220Ω;1005 | R_US | Resistor_SMD:R_0402_1005Metric | Resistor, US symbol
R7, | 1 | 560Ω;1608 | R_US | Resistor_SMD:R_0603_1608Metric | Resistor, US symbol
R9, R10, R11, R12, R56, | 5 | 0Ω;3216 | SHUNT | Resistor_SMD:R_1206_3216Metric | 0 Ohme Power shunt
R13, | 1 | 100KΩ;1608 | R_US | Resistor_SMD:R_0603_1608Metric | Resistor, US symbol
R14, R15, R16, R18, R19, R21, R22, R23, R24, R43, R47, R48, R49, R50, R51, R52, R53, R54, R55, | 19 | 100KΩ;1005 | R_US | Resistor_SMD:R_0402_1005Metric | Resistor, US symbol
R17, R44, | 2 | 1KΩ;1005 | R_US | Resistor_SMD:R_0402_1005Metric | Resistor, US symbol
R25, R26, | 2 | .16Ω.25W;2012 | R_US | Resistor_SMD:R_0805_2012Metric | Resistor, US symbol
R27, R28, R29, R30, R31, R32, R33, R34, R35, R36, R37, R38, R39, R40, R41, R42, | 16 | 270Ω;1608 | R_US | Resistor_SMD:R_0603_1608Metric | Resistor, US symbol
R45, | 1 | 2.2KΩ;1005 | R_US | Resistor_SMD:R_0402_1005Metric | Resistor, US symbol
R46, | 1 | 3.3KΩ;1005 | R_US | Resistor_SMD:R_0402_1005Metric | Resistor, US symbol
R57, | 1 | 120Ω;1005 | R_US | Resistor_SMD:R_0402_1005Metric | Resistor, US symbol
R58, R59, | 2 | 120Ω.25W;3216 | R_US | Resistor_SMD:R_1206_3216Metric | Resistor, US symbol
R60, R61, | 2 | 300Ω;1608 | R_US | Resistor_SMD:R_0603_1608Metric | Resistor, US symbol
SW1, SW2, | 2 | BUTTON;6x6 | SW_Push | Button_Switch_SMD:SW_Push_1P1T_NO_6x6mm_H9.5mm | Push button switch, generic, two pins
TP1, | 1 | USB5V;TP | TestPoint | TestPoint:TestPoint_THTPad_1.5x1.5mm_Drill0.7mm | test point
TP2, TP3, TP4, TP5, TP6, TP8, | 6 | GND;TP | TestPoint | TestPoint:TestPoint_THTPad_1.5x1.5mm_Drill0.7mm | test point
TP7, | 1 | 3.3V;TP | TestPoint | TestPoint:TestPoint_THTPad_1.5x1.5mm_Drill0.7mm | test point
TP9, | 1 | P5V;TP | TestPoint | TestPoint:TestPoint_THTPad_1.5x1.5mm_Drill0.7mm | test point
TP10, | 1 | 5V;TP | TestPoint | TestPoint:TestPoint_THTPad_1.5x1.5mm_Drill0.7mm | test point
TP11, | 1 | 9V;TP | TestPoint | TestPoint:TestPoint_THTPad_1.5x1.5mm_Drill0.7mm | test point
TP12, | 1 | SBC_TX;TP | TestPoint | TestPoint:TestPoint_THTPad_1.5x1.5mm_Drill0.7mm | test point
TP13, | 1 | SBC_RX;TP | TestPoint | TestPoint:TestPoint_THTPad_1.5x1.5mm_Drill0.7mm | test point
TP14, | 1 | WOW_TX;TP | TestPoint | TestPoint:TestPoint_THTPad_1.5x1.5mm_Drill0.7mm | test point
TP15, | 1 | WOW_RX;TP | TestPoint | TestPoint:TestPoint_THTPad_1.5x1.5mm_Drill0.7mm | test point
TP16, | 1 | ~NESTOP_SET~;TP | TestPoint | TestPoint:TestPoint_THTPad_1.5x1.5mm_Drill0.7mm | test point
TP17, | 1 | ~NWOW_ESTOP~;TP | TestPoint | TestPoint:TestPoint_THTPad_1.5x1.5mm_Drill0.7mm | test point
U1, U2, U3, | 3 | LM5050-1;TSOT-23-6 | LM5050-1;TSOT-23-6 | Package_TO_SOT_SMD:TSOT-23-6 | Idealf Diode w/external NFET
U4, | 1 | MCP7940;SOIC8 | MCP7940;SOIC8 | Package_SO:SOIC-8_3.9x4.9mm_P1.27mm
U5, | 1 | CAT24C32;SOIC8 | CAT24C32;SOIC8 | Package_SO:SOIC-8_3.9x4.9mm_P1.27mm | 32Kb I2C EEPROM
U6, | 1 | DRV8833PWPR;HTSSOP16EP3.4x5 | DRV8833PWPR;HTSSOP16EP3.4x5 | Package_SO:HTSSOP-16-1EP_4.4x5mm_P0.65mm_EP3.4x5mm_Mask3x3mm_ThermalVias | DualH-Bridge Motor Drive
U7, U8, U9, U13, | 4 | SN74HC595;TSSOP16 | SN74HC595;TSSOP16 | Package_SO:TSSOP-16_4.4x5mm_P0.65mm | Tri-State 8-Bit Shift Register
U10, U11, | 2 | CD4504B;TTSOP16 | CD450B;TTSOP16 | Package_SO:TSSOP-16_4.4x5mm_P0.65mm | Hex Level Shifter
U12, | 1 | ACS711;SOIC8 | ACS711;SOIC8 | Package_SO:SOIC-8_3.9x4.9mm_P1.27mm
U14, U15, | 2 | SN74HC165;TSSOP16 | SN74HC165;TSSOP16 | Package_SO:TSSOP-16_4.4x5mm_P0.65mm | 8-Bit Parallel In Serial Out Shift Register
U16, U17, | 2 | 74x11G1;TSOP6 | 74x11G1 | Package_SO:TSOP-6_1.65x3.05mm_P0.95mm | Triple 3-input AND
U18, U19, | 2 | MCP2542;SOIC8 | MCP2542;SOIC8 | Package_SO:SOIC-8_3.9x4.9mm_P1.27mm | MCP2542
U20, | 1 | 74LVC1G74;TSSOP8 | 74LVC1G74;TSSOP8 | Package_SO:TSSOP-8_3x3mm_P0.65mm | D-type flip-flop edge-trigger/set/reset
U21, U22, | 2 | CPC1017N;SOP4W3.8L4.1 | CPC1017N;SOP4W3.8WL4.1 | Package_SO:SOP-4_3.8x4.1mm_P2.54mm | CPC1017 Solid State Relay
VR1, | 1 | AMS1117-3.3V800mA_GOI;SOT223 | AMS1117-3.3V800mA_GOI;SOT223 | Package_TO_SOT_SMD:SOT-223-3_TabPin2 | 3.3V 800mA LDO Voltage Linear Regulator
X1, | 1 | 32.768kHz12.5pF;3.2x1.5 | Crystal | Crystal:Crystal_SMD_3215-2Pin_3.2x1.5mm | Two pin crystal

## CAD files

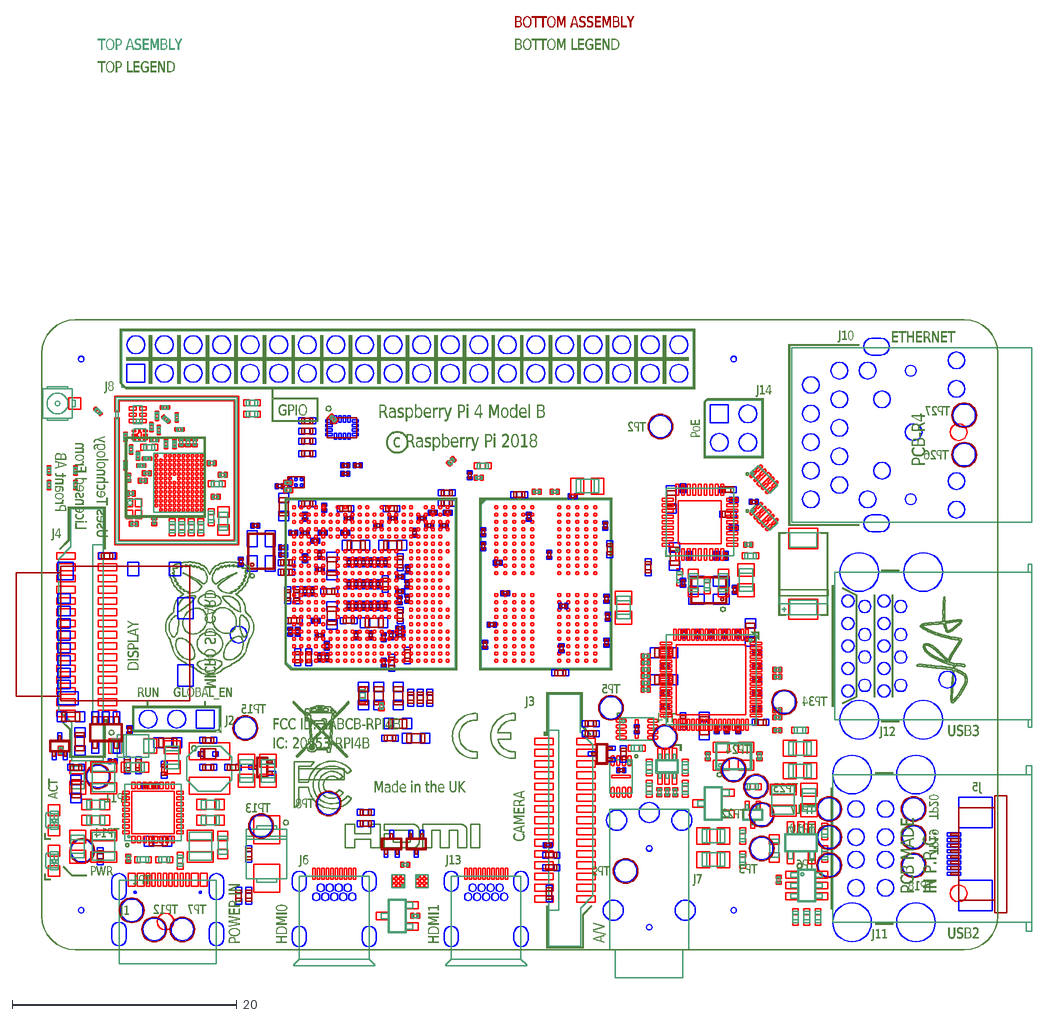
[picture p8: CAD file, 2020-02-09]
mechanical/dxf/rpi_MECH_4b_4p0.dxf
TP20
TP19
TP18
TP17
TP10
TP6
TP5
TP34
TP15
TP14
TP13
TP11
TP8
TP7
TP24
TP23
TP22
TP12
TP9
TP4
TP3
TP2
TP1
TP27
TP26
J5
Made in the UK
IN P.R.C.
PCB MADE
IC: 20953-RPI4B
FCC ID: 2ABCB-RPI4B
PCB-R4
RUN
GLOBAL_EN
Proant AB
Licensed From
Uses Technology
MICRO SD CARD
GPIO
c Raspberry Pi 2018
Raspberry Pi 4 Model B
J2
J8
J14
J11
J12
J10
J7
J13
J3
J6
J1
J4
PoE
USB3
USB2
ETHERNET
A/V
DISPLAY
CAMERA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

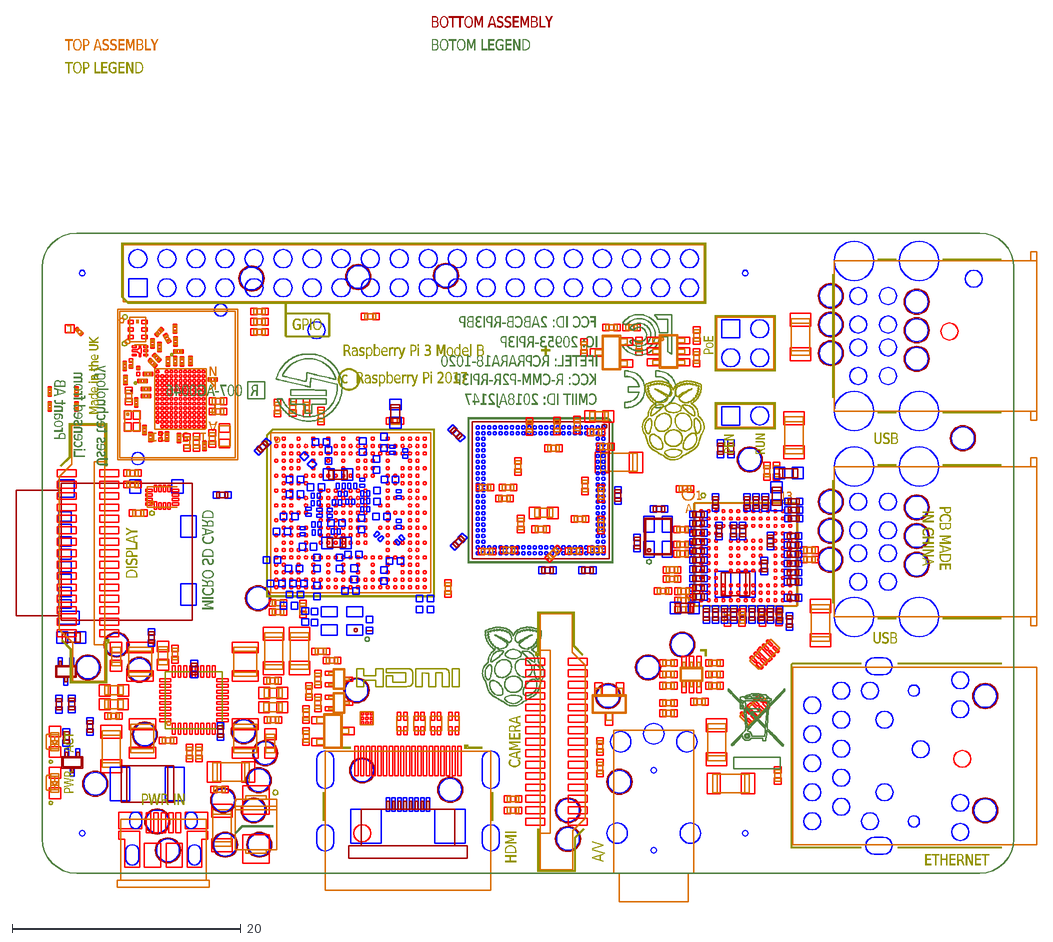
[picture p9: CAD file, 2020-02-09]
mechanical/dxf/rpi_MECH_3bplus.dxf
11
5
1
N
K
E
A
13
R 007-AG0046
CMIIT ID: 2018AJ2147
KCC: R-CMM-P2R-RPI3P
IFETEL: RCPRARA18-1020
IN CHINA
PCB MADE
PEN
IC: 20953-RPI3P
FCC ID: 2ABCB-RPI3BP
Licensed from
Proant AB
Uses technology
PoE
c Raspberry Pi 2017
Raspberry Pi 3 Model B
MICRO SD CARD
HDMI
BOTOM LEGEND
BOTTOM ASSEMBLY
TOP LEGEND
TOP ASSEMBLY
Made in the UK
A/V
GPIO
USB
ETHERNET
PWR IN
DISPLAY
CAMERA
RUN
ACT
PWR

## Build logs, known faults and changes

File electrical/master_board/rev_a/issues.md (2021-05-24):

<!-- ===================================== 100 characters ====================================== -->

# Master Board Rev. A Issues

1.  JLCPCB had issues with C1 footprint.  They were soldered in anyhow.
2.  JLCPCB had issues with SW1/SW2 footprint.  They were soldered in anyhow.
3.  JP1 and JP8 have simliar labels.  One is for the Ring LED's and the
    other is for the power indicator LED's.
4.  The encoder M1x2RA pins are offset by 1.in.
    Both need to be offset outward by 1. in.
5.  The assembly orders is:
    1. Empty motor holder installed into Romi Base.
    2. Raspberry Pi bolted to Romi Base.
    3. Master Board is plugged onto Romi Base and bolted onto
       appropriate stand-offs.
    4. The encoder board is soldered to the motor gear motor.
    5. The encoder/gearmotor sub-assembly is slide into the motor holder.

    The issue is that the Master PCB is too high to allow the
    motor holder tabs to deflect.
6.  The Pololu regulators problems:
    1. They are 12V instead of 9V.
7.  Power Indicator LED's are way too bright.
8.  The JLCPCB order of the ideal diodes got some part other than the LM5050.
9.  The LM5050 does not guarantee to work under 5V, so we may need to
    find another component.
10. There needs to be a little more clearance for the encoder magnets.
11. There is no clearance for the WOW connector on top.
    Move to a different location.
    For now, mount on the bottom.
12. There are solder bumps for the ST-link board.
13. Investigate through hole connectors for Sonars.
14. Get shorter eletrolytic capacitors.  For now tilt them on edge.
15. ST-Link...
16. WOW connector...
17. LD06 ...
18. Bottom Sonars...
19. Top Sonar ...
20. Boost converter clearance ...
21. Capacitors ...
22. The 5 top sonar footprints are all rotated 180 degrees and point the wrong directions.
    The 2 bottom sonar footprints are correct.
23. Wheel clearance is tight.  The Nucleo spacers need to be lifted up by about 3/16 inch.
    In other words -- 1/2" plus 3/16".
24. The motor driver needs a .1µF capacitor between pin-11 (VCP) and pin-12 (VM).
25. The ESTOP LED is inverted.  It should be ON for an ESTOP not OFF.
26. The RxD and TxD pins on U19 are swapped.
27. There is something weird going on with power coming in from the ST-Link USB connector
    event when the Nucleo is powered by E5V jumper.
28. The right encoder is rotated 180 degrees along the Z-axis  and is incompatible with the
    associated encoder.
29. The labels on the encoder signals are swapped.  LQUAD_A/LQUAD_B are connected to the
    right motor/encoder and RQUAD_A/RQUAD_B are connected to the left encoder.
30. The serial port on the microcontroller is connected to the console pins on the RasPi4.
    This is a mistake.  Instead, use UART5 on the RasPi4.  
31. The Motor controller will start with motors at full speed on power-up.  Add pull-down/pull-up
    resistors to the two CTL pins for each motor to force them into a known (and safe) state when
    starting up.  Likewise the SLEEP pin needs a power-up pull-up/down resistor to put it into a
    known state on power up.
32. UART3 can be connected to either the ST-LINK or the Morpho Pins:
    * STLK_TX (Nucleo Scehmatic Name):
      * ST-Link:
        * U2-Pin 12
	* CN5:TX (Upper)
      * Nucleo:
        * PD9
        * U8B-Pin 78
	* USART3_RX
        * SB6 Closed=>ST-Link    <==== Open SB6
        * SB4 Closed=>Morpho CN11-69
      * Pi4
        * TXD3: Pin 7
    * STLK_RX (Nucleo Scehmatic Name):
      * ST-Link:
        * U2-Pin 13:
	* CN5: RX (Lower)
      * Nucleo:
        * PD8
        * U8B-Pin 77
	* USART3_TX
	* SB5 Closed=>ST-Link
	* SB7 Closed=>Morpho CN12-10
      * Pi 4
        * RXD3 Pin 29
33. PB4 is connected to LMOTOR_CTL1.  On startup, PB is conne NJTRST and is an output that
    is set to high.  That causes the right motor to go full speed until the initialization
    code gets around to converting into a GPIO in the low state.  Pull down resistors do
    not help.  The pins that do not initialize to floating are described in section 6.3.1
    in the reference manual (page 223.)  The PA15 and PB4 are not suitable.  PB4 is currently
    used as TIM3_CH4.  The correct thing to a timer that does not use PBB or PBA15 ***AND***
    connect pull down resistors to the LMOTOR/RMOTOR_CTL1/2 pins.

<!--
7: TXD3(Pi4)             Avail
8: TXD0 or TXD1(Pi4)     SBC_TX
10: RXD0 or RXD1(Pi4)    SBC_RX
21: RXD4 (Pi4)           Avail
24: TXD4 (Pi4)           SBC_ALIVE
27: TXD2 (Pi4)           ID_SDA
28: RXD2 (Pi4)           ID_SCL
29: RXD3 (Pi4)           Avail
32: TXD5 (Pi4)           Avail (Wired to USART1)
33: RXD5 (Pi4)           Avail (Wired to USART1)

RasPi4:
* Pin 8  => TXD1
* Pin 10 <= RXD1

* Pin 32 TXD5 => SBC_TX
* Pin 33 RXD5 <= SBC_RX

Master Board:
* PB15 USART1_RX CN12-17 <= SBC_TX
* PB6  USART1_TX CN12-26 => SBC_RX

-->

## Wire Patches

1. Bridge E5V to 5V: (CN11:6 Nucleo) <=> (CN10:1 Sonar)
2. Bridge NW:3V to Center:3V: (Via near U19:5 and R59) <=> (Via near C23 and U20:7/8)
3. Bridge NW:P5V to SW:P5V: (P5V: NW Back Edge trace <=> P5V: SW Back Edge Trace)
4. Bridge NE:P5V to SE:P5V: (P5V: NE Back Edge trace <=> P5V: SE Back Edge Trace)
5. Bridge NW:9V to SW:9V: (P5V: NW Back Edge trace <=> P5V: SW Back Edge Trace)
6. Bridge NE:9V to SE:9V: (P5V: NE Back Edge trace <=> P5V: SE Back Edge Trace)
7. Bridge NW:LED_GND to GND: (LED_GND:Via Near SW motor well inside corner <=> GND:Via near D11:1)
8. Bridge NE:LED_GND to GND: (LED_GND:Via Near R40 <=> GND:Via radially in from R40 one.)
9. Bridge NW:LED_GND to GND: (LED_GND:Via Near SW motor well inside corner <=> GND:Via near D11:1)
10. Bridge NE:LED_GND to GND: (LED_GND:Via Near R40 <=> GND:Via radially in from R40 one.)

## Spacers and Standoffs

The various levels are held together using spacers and standoffs.
#2-56 threaded spacers and standoffs are used wish some occassional washers inserted
to do find adjustment of the height.
A spacer is threaded all of the way through.
A stand-off has a threaded hole on one side and screw thread on the other.

Shorter spacers and standoffs can be screwed together to make longer spacers and standoffs.
A longer standoff is made up entirely out of shorter standoffs.
A longer spacer is made up one spacer and one or more standoffs.
The goal is to figure out which spacers/standoffs to use.

### Robot Levels

There are 6 robot levelst are listed below from lowest to highest:

* Base Level:
  The base level is the lowest level of the Romi Base.

* Battery Level:
  The battery level is the top of the battery compartment of the Romi Base.

* SBC Level:
  The SPC level is the bottom surface of the SBC (Single Board Computer)

* Master Board:
  The master board has two surfaces that correspond to the top and bottom surfaces
  of the master board.

* Nucleo Board:
  The Nucleo board is attached to the top of the Master board.

* Arm Base:
  The Arm shelf also has two surfaces that correspond to the top/bottom of Arm base.

* Lidar/Battery Base:
  The LIDAR battery base two surfaces.  The Lidar and Battery are mounted on the top surface.

## Inter Level Requirements:

* Base to SBC Level Spacer (18.2mm - 2.5mm = 15.7): 
  2 spacers are needed.

* Battery to SBC Level Spacer (6.35mm = 1/4in):
  2 spacers are needed.

* Base to Master Bottom Spacer (28.40mm)
  4 spacers are needed.

* Master Top to Nucleo Bottom Spacer (13mm)
  4 spacers are needed
  1 standoff is needed (for alignment)

* Master Top to Arm Bottom Standoff * Spacer (33.3mm)
  There are two standoffs needed and 2 spacers needed per robot.

* Arm Top to Lidar/Battery bottom standoff: (3in = 3 * 25.4mm = 76.2mm)
  2 stand-offs are needed.

* Master Top to Lidar/Battery bottom standoff (33.3mm + 2.5mm + 76.2mm = 108.4mm)
  2 stand-offs are needed.

## Misc:

1. Jumper positions:
   JP1 1x3 SW Power indicator LED's Enable Near 3.3V reguator
   JP2 1x2 SW 5V Shunt Near power connectors
   JP3 1x2 NE 9V Shunt Near Camera Slot
   JP4 1x2 SW 3.3V Shunt Near 3.3V regulators and arm slot
   JP5 1x2 SW P5V Shunt above 5V Shunt JP2
   JP6 1x3 SW Rasp Pi Display control Near voltage test points
   JP7 1x2 NW I2C program Near Pi Processor Heat sink slot
   JP8 1x3 SW LED's enable Near D20 LED
   JP9 1x2 NW ESTOP Near button.
2. Test Point positions:
   TP1 USB5V SW Near RasPi
   TP2 GND NE C3
   TP3 GND NE RPi Camera slot
   TP4 GND NE Back corner
   TP5 GND NW Back corner
   TP6 GND SE Near Q3 Q6
   TP7 3.3V SW Power TP's
   TP8 GND SW Power TP's
   TP9 P5V SW Power TP's
   TP10 5V SW Power TP's
   TP11 9V SW Power TP's
   TP12 SBC_TX SW Near Raspi
   TP13 SBC_RX SW Near Raspi
   TP14 WOW_TX NW Near Inside edge
   TP15 WOW_RX NW Near Wheel Well
   TP16 ~NESTOP_SET~ NE Near inside edge
   TP17 ~NWOW_ESTOP~ NW Near Wheel Well

## Board Work

### Board A

* RTC Battery
* Nulceo Alignment spacer

### Board B

* Fix diode D14
* Pololu Boost Supply
* Wow headers
* I2C EEProm header
* Electrolytic capacitors
* Center Sonar
* Bottom Sonars
* 8 Edge detector sonars
* RTC Battery
* RasPi Display Power Header
* Missing Encoder F1x3

### Board C

* Pololu Boost Supply
* Wow headers
* I2C EEProm header
* Electrolytic capacitors
* Center Sonar
* Bottom Sonars
* 8 Edge detector sonars
* RTC Battery
* RasPi Display Power Header

### Board D

* Pololu Boost Supply
* Wow headers
* I2C EEProm header
* Electrolytic capacitors
* Center Sonar
* Bottom Sonars
* 8 Edge detector sonars
  * Solder suck 2 holes
* RTC Battery
* RasPi Display Power Header

### Board E

By accident, nucleo is soldered to female connector.
No further work on E until (if) this if resolved.

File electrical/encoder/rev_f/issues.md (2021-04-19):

# Encoders Rev F Issues

* No issues yet.

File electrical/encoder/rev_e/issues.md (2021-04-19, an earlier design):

# Encoders Rev E Issues

* No issues yet.

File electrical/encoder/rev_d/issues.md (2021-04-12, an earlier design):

# Encoders Rev D Issues

* No issues yet.

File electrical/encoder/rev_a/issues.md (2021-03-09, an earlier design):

# Encoder Rev. A Issues

The connectors misplaced inside by .1 inch.

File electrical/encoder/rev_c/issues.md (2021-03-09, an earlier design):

# Encoders Rev B Issues

* The motor hub is 5mm in diamter.  A #6 drill work for enlarging the hole.
* It may make sense to use one of the Pololu encoders to figure out what radius
  the used to center the hall effect sensors.
* Use an 0603 resistor for the pull-up resistor.

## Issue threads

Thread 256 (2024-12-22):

Google Website Link Broken

RufusVS, 2024-12-22:
This group may be defunct, but I thought I'd bring this up in case it wasn't and should be redirected.

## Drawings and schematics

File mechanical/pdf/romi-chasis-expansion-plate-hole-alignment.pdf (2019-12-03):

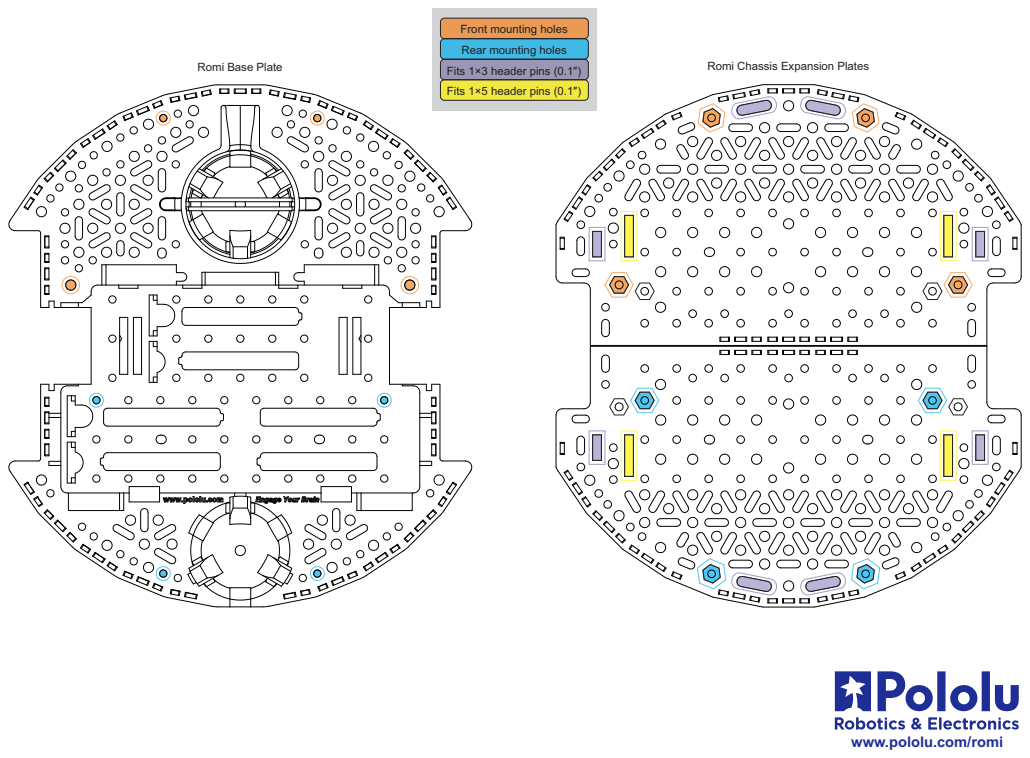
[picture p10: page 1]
Romi Base Plate; Fits 1×3 header pins (0.1″); Romi Chassis Expansion Plates

Front mounting holes
Rear mounting holes

Fits 1×5 header pins (0.1″)

www.pololu.com/romi

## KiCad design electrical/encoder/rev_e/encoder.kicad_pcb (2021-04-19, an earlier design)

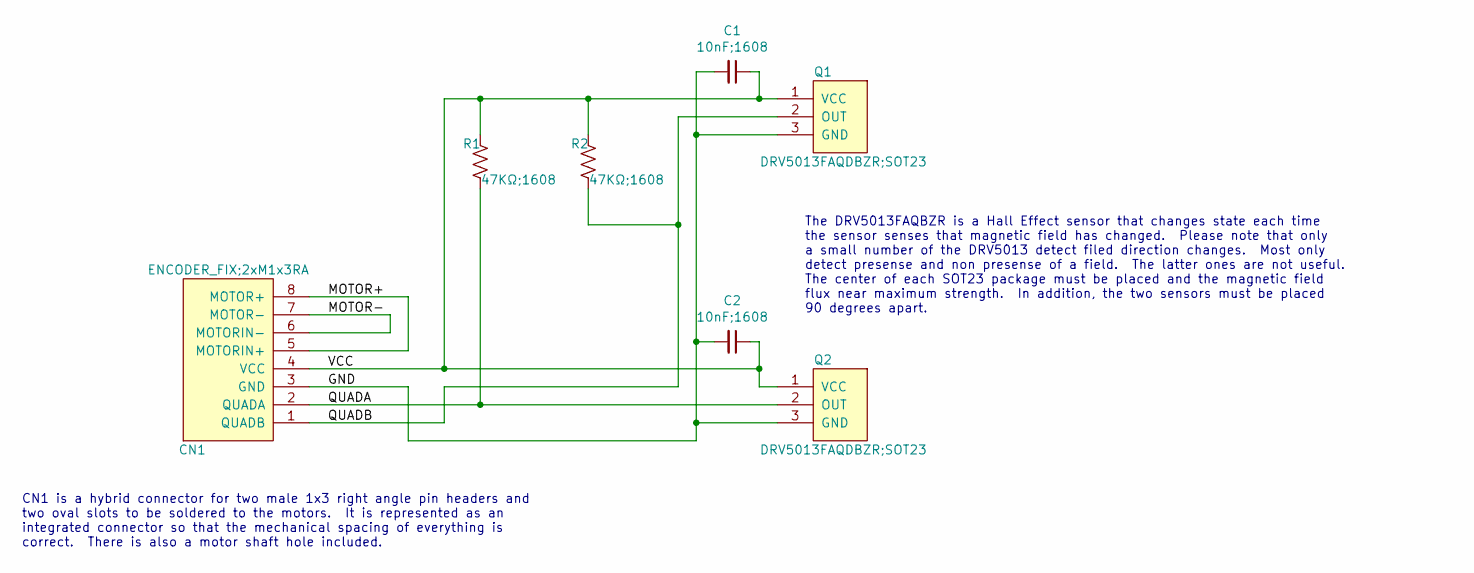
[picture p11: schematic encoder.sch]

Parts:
C1, C2: 10nF;1608; C_0603_1608Metric
CN1: ENCODER_FIX;2xM1x3RA; ENCODER_2xM1x3RA
Q1, Q2: DRV5013FAQDBZR;SOT23; SOT-23
R1, R2: 47KΩ;1608; R_0603_1608Metric

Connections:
/GND: C1.2, C2.2, CN1.3 (GND), Q1.3 (GND), Q2.3 (GND)
/MOTOR+: CN1.5 (MOTORIN+), CN1.8 (MOTOR+)
/MOTOR-: CN1.6 (MOTORIN-), CN1.7 (MOTOR-)
/QUADA: CN1.2 (QUADA), Q2.2 (OUT), R1.2
/QUADB: CN1.1 (QUADB), Q1.2 (OUT), R2.2
/VCC: C1.1, C2.1, CN1.4 (VCC), Q1.1 (VCC), Q2.1 (VCC), R1.1, R2.1

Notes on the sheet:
The DRV5013FAQBZR is a Hall Effect sensor that changes state each time the sensor senses that magnetic field has changed. Please note that only a small number of the DRV5013 detect filed direction changes. Most only detect presense and non presense of a field. The latter ones are not useful. The ce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
CN1 is a hybrid connector for two male 1x3 right angle pin headers and two oval slots to be soldered to the motors. It is represented as an integrated connector so that the mechanical spacing of everything is correct. There is also a motor shaft hole included.

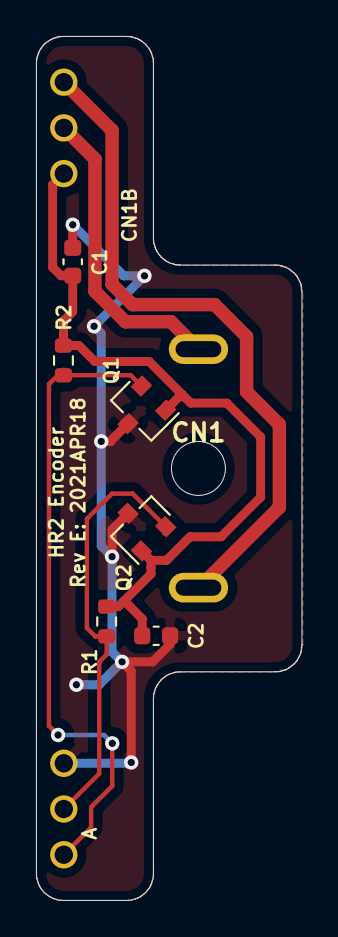
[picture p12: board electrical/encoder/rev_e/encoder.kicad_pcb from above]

Board: 2 copper layers, 14.8 x 48.0 mm, 7 parts (0 on the bottom side), 6 nets.

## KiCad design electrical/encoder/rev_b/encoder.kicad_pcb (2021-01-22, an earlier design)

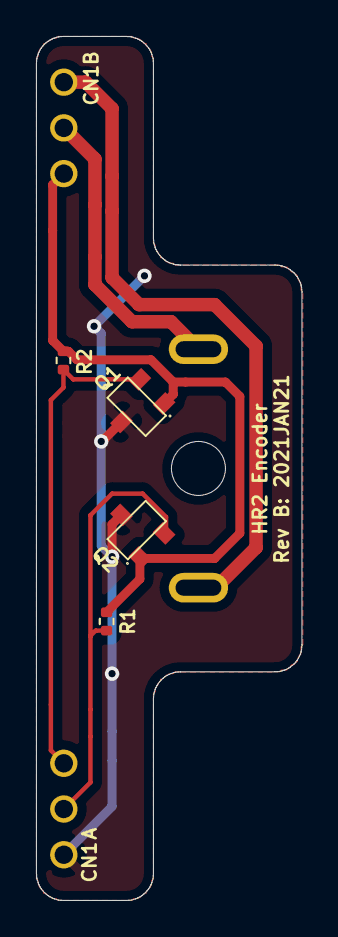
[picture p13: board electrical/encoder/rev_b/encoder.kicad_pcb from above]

Board: 2 copper layers, 14.8 x 48.0 mm, 5 parts (0 on the bottom side), 6 nets.

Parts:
CN1: ENCODER;2xM1x3RA; ENCODER_2xM1x3RA
Q1, Q2: AH1806;SC59; SC59
R1, R2: 100Ω;1005; R_0402_1005Metric

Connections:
/GND: CN1.1, Q1.2, Q2.2
/MOTOR+: CN1.5, CN1.8
/MOTOR-: CN1.6, CN1.7
/QUADA: CN1.2, Q2.3, R1.2
/QUADB: CN1.3, Q1.3, R2.2
/VCC: CN1.4, Q1.1, Q2.1, R1.1, R2.1

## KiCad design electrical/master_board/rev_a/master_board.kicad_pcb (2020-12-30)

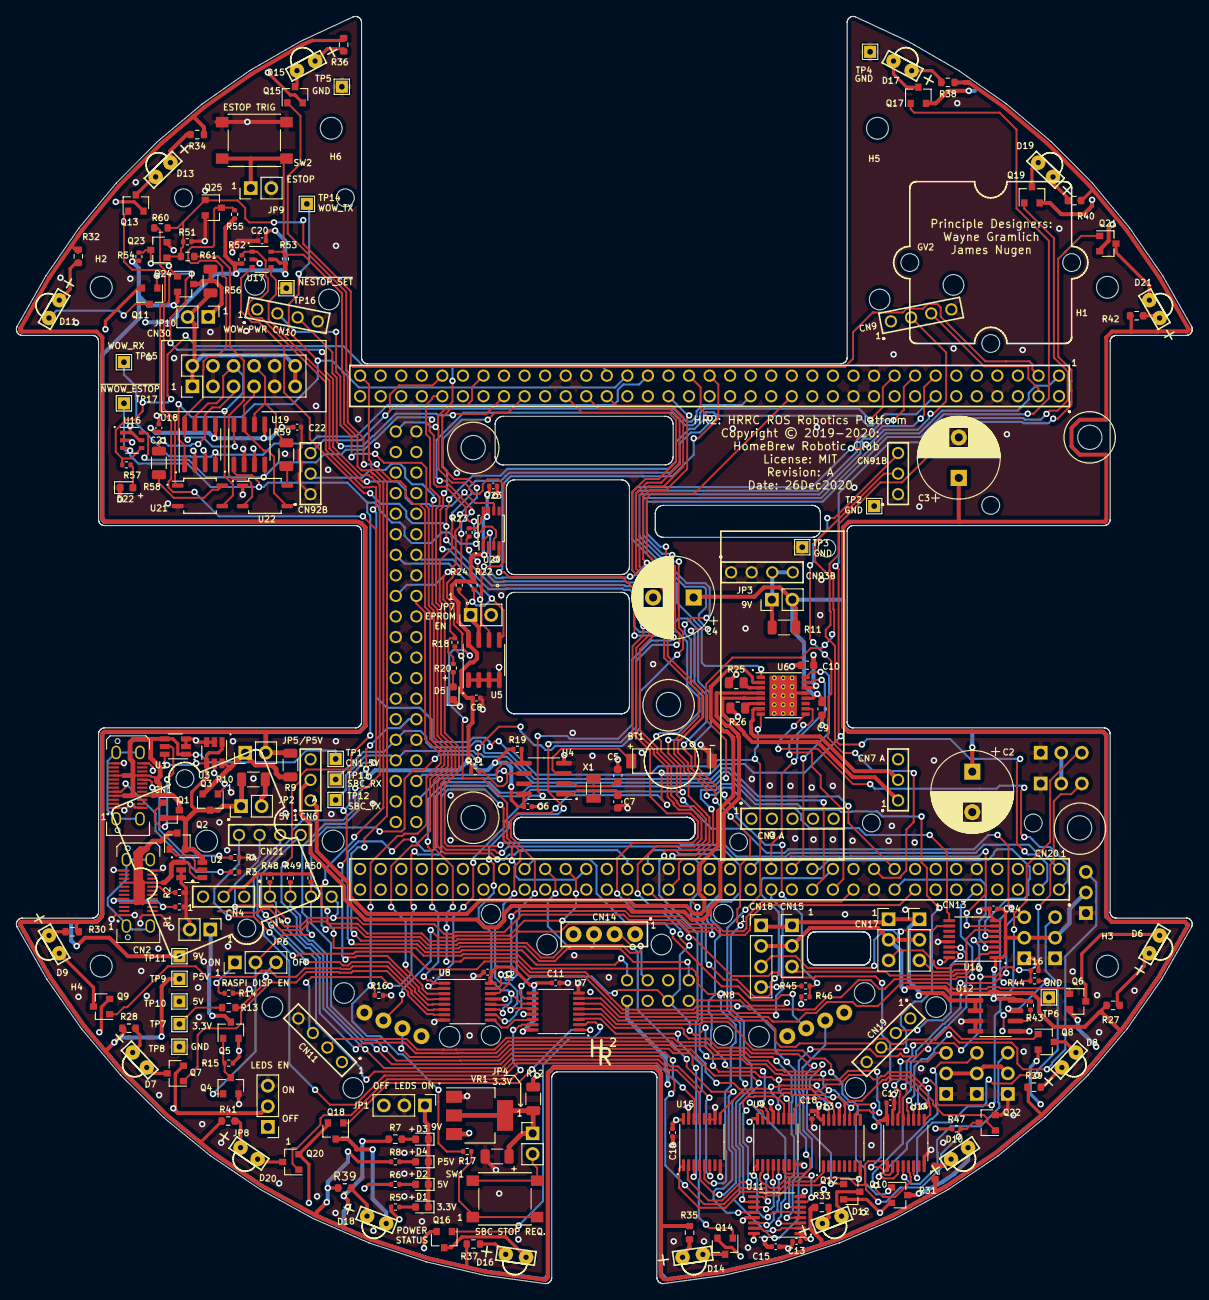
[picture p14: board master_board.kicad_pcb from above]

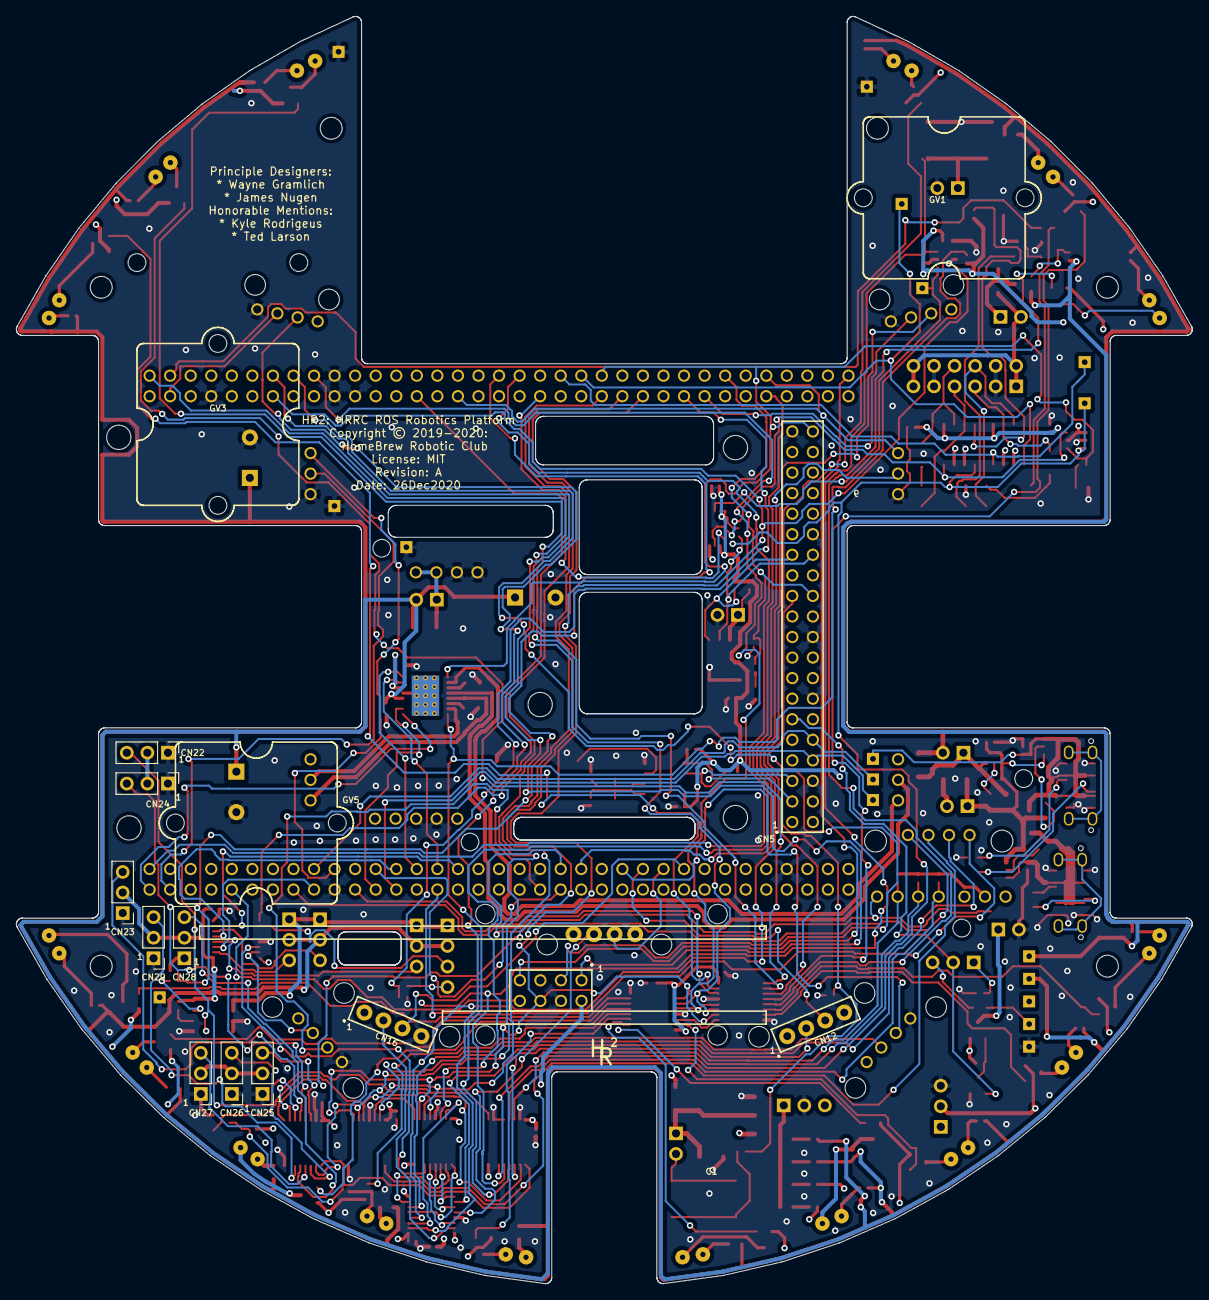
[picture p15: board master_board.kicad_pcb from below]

Board: 4 copper layers, 145.3 x 156.6 mm, 226 parts (13 on the bottom side), 198 nets.

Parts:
BT1: COIN_HOLDER6.8R;TE1376164-1; TE1376164-1_COINHOLDER6.8
C1: Ta22µF6.3V;3216; C_1206_3216Metric
C2, C4: 470µF,25Vmin;D10P5H13max; CP_Radial_D10.0mm_P5.00mm
C3: 1000µF@10Vmin;D10P5H13max; CP_Radial_D10.0mm_P5.00mm
C5, C7: 15pF;1608; C_0603_1608Metric
C6, C8, C11, C12, C13, C14, C15, C17, C18, C19, C20, C21, C22, C23: 0.1µF;1005; C_0402_1005Metric
C9: 10µF;1608; C_0603_1608Metric
C10: 2.2µF6.3V;1608; C_0603_1608Metric
C16: 0.01µF;1005; C_0402_1005Metric
CN1: USB-C;USB-C,POGND; USB_C_Receptacle_JAE_DX07S024WJ3R400
CN2: USB-C;USB-C; USB_C_Receptacle_JAE_DX07S024WJ3R400
CN3: POLOLU_U3V70F9;F1x4+F1x5; U3V70xMATE_F1x4+F1x5
CN4: RPI_DSP_PWR;M1x2; PinHeader_1x02_P2.54mm_Vertical
CN5: RASPI;F2X20; RASPI_F2X20
CN6, CN7: HR2_ENCODER;2xF1x3; ENCODER_2xF1x3
CN8: STADAPTER;F2x4; STADAPTER_F2x4
CN9, CN10: HCSR04LP;F1X4; HCSR04_F1x4H
CN11, CN19: HCSR04LP;F1X4; HCSR04_F1x4
CN12, CN14, CN16: HCSR04LP;F1X4; HCSR04_F1x4LP
CN13, CN15, CN17: SERVO;M1x3; PinHeader_1x03_P2.54mm_Vertical
CN18: SERVO;M1x4; PinHeader_1x04_P2.54mm_Vertical
CN20: NUCLEO-F767ZI;2xF2x35; NUCLEO_F767ZI_2xF2x35
CN21: LIDAR_ADAPTER;2xF1x4_F1x3; LIDAR_ADAPTER_2xF1x4_F1x3
CN22, CN23, CN24, CN25, CN26, CN27, CN28, CN29: SENSE;M1x3; PinHeader_1x03_P2.54mm_Vertical
CN30: WOW_OUT;M2x6S; PinHeader_2x06_P2.54mm_Vertical_Shrouded
D1, D2, D3, D4, D5: LEDGRN;1608; LED_0603_1608Metric
D6, D7, D8, D9, D10, D11, D12, D13, D14, D15, D16, D17, D18, D19, D20, D21: LED;GRNRA; LED_GRNRA
D22: REDLED;1608; LED_0603_1608Metric
GV1, GV2, GV3, GV4, GV5: GROVE;20x20; GROVE20x20
H1, H2, H3, H4, H5, H6: HOLE;M2.5; MountingHole_2.7mm_M2.5
JP1, JP8: LED_EN;M1x3; PinHeader_1x03_P2.54mm_Vertical
JP2, JP3, JP4, JP5, JP10: SHUNT;M1x2; PinHeader_1x02_P2.54mm_Vertical
JP6: RPI_DISP_EN;M1x3; PinHeader_1x03_P2.54mm_Vertical
JP7: JUMPER;M1x2; PinHeader_1x02_P2.54mm_Vertical
JP9: EXT_ESTOP;M1x2; PinHeader_1x02_P2.54mm_Vertical
Q1, Q2, Q3: NFET_3A_GSD;SOT23; SOT-23
Q4, Q6, Q7, Q8, Q9, Q10, Q11, Q12, Q13, Q14, Q15, Q16, Q17, Q18, Q19, Q20, Q21, Q22, Q23, Q25: 2N7002;SOT23; SOT-23
Q5, Q24: PFET_6A_GSD;SOT23; SOT-23
R1, R2, R3, R4: 10KΩ;1005; R_0402_1005Metric
R5, R20: 33Ω;1005; R_0402_1005Metric
R6, R8: 220Ω;1005; R_0402_1005Metric
R7: 560Ω;1608; R_0603_1608Metric
R9, R10, R11, R12, R56: 0Ω;3216; R_1206_3216Metric
R13: 100KΩ;1608; R_0603_1608Metric
R14, R15, R16, R18, R19, R21, R22, R23, R24, R43, R47, R48, R49, R50, R51, R52, R53, R54, R55: 100KΩ;1005; R_0402_1005Metric
R17, R44: 1KΩ;1005; R_0402_1005Metric
R25, R26: .16Ω.25W;2012; R_0805_2012Metric
R27, R28, R29, R30, R31, R32, R33, R34, R35, R36, R37, R38, R39, R40, R41, R42: 270Ω;1608; R_0603_1608Metric
R45: 2.2KΩ;1005; R_0402_1005Metric
R46: 3.3KΩ;1005; R_0402_1005Metric
R57: 120Ω;1005; R_0402_1005Metric
R58, R59: 120Ω.25W;3216; R_1206_3216Metric
R60, R61: 300Ω;1608; R_0603_1608Metric
SW1, SW2: BUTTON;6x6; SW_Push_1P1T_NO_6x6mm_H9.5mm
TP1: USB5V; TestPoint_THTPad_1.5x1.5mm_Drill0.7mm
TP2, TP3, TP4, TP5, TP6, TP8: GND; TestPoint_THTPad_1.5x1.5mm_Drill0.7mm
TP7: 3.3V; TestPoint_THTPad_1.5x1.5mm_Drill0.7mm
TP9: P5V; TestPoint_THTPad_1.5x1.5mm_Drill0.7mm
TP10: 5V; TestPoint_THTPad_1.5x1.5mm_Drill0.7mm
TP11: 9V; TestPoint_THTPad_1.5x1.5mm_Drill0.7mm
TP12: SPC_TX;M1x2; TestPoint_THTPad_1.5x1.5mm_Drill0.7mm
TP13: SBC_RX;M1x2; TestPoint_THTPad_1.5x1.5mm_Drill0.7mm
TP14: WOW_TX;M1x1; TestPoint_THTPad_1.5x1.5mm_Drill0.7mm
TP15: WOW_RX;M1x1; TestPoint_THTPad_1.5x1.5mm_Drill0.7mm
TP16: ~nESTOP_SET; TestPoint_THTPad_1.5x1.5mm_Drill0.7mm
TP17: ~nWOW_ESTOP;M1x1; TestPoint_THTPad_1.5x1.5mm_Drill0.7mm
U1, U2, U3: LM5050-1;TSOT-23-6; TSOT-23-6
U4: MCP7940;SOIC8; SOIC-8_3.9x4.9mm_P1.27mm
U5: CAT24C32;SOIC8; SOIC-8_3.9x4.9mm_P1.27mm
U6: DRV8833PWPR;HTSSOP16EP3.4x5; HTSSOP-16-1EP_4.4x5mm_P0.65mm_EP3.4x5mm_Mask3x3mm_ThermalVi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
U7, U8, U9, U13: SN74HC595;TSSOP16; TSSOP-16_4.4x5mm_P0.65mm
U10, U11: CD4504B;TTSOP16; TSSOP-16_4.4x5mm_P0.65mm
U12: ACS711;SOIC8; SOIC-8_3.9x4.9mm_P1.27mm
U14, U15: SN74HC165;TSSOP16; TSSOP-16_4.4x5mm_P0.65mm
U16, U17: 74x11G1;TSOP6; TSOP-6_1.65x3.05mm_P0.95mm
U18, U19: MCP2542;SOIC8; SOIC-8_3.9x4.9mm_P1.27mm
U20: 74LVC1G74;TSSOP8; TSSOP-8_3x3mm_P0.65mm
U21, U22: CPC1017N;SOP4W3.8L4.1; SOP-4_3.8x4.1mm_P2.54mm
VR1: AMS1117-3.3V800mA_GOI;SOT223; SOT-223-3_TabPin2
X1: 32.768kHz12.5pF;3.2x1.5; Crystal_SMD_3215-2Pin_3.2x1.5mm

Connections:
/3.3V: C6.1, C8.2, C11.1, C12.1, C13.1, C14.1, C15.1, C17.1, C18.1, C19.1, C20.2, C21.2, C22.2, C23.2, CN8.1, CN21.2, CN22.2, CN23.2, CN24.2, CN25.2, CN26.2, CN27.2, CN28.2, CN29.2, JP4.2, R5.1, R12.2, R13.1, R19.1, R21.1, R22.1, R23.1, R24.1, R43.1, R47.1, R48.1, R49.1, R50.1, R52.1, R53.1, R55.1, SW1.2, TP7.1, U4.8, U5.8, U7.16, U8.16, U9.16, U10.1, U11.1, U12.8, U13.16, U14.16, U15.16, U16.1, U16.5, U17.5, U18.5, U19.5, U20.2, U20.7, U20.8
/5V: CN3.4, CN3.5, CN5.2, CN5.4, CN6.3, CN7.3, CN9.1, CN10.1, CN11.1, CN12.1, CN14.1, CN16.1, CN19.1, CN20.1124, CN20.1207, CN21.1, JP2.2, Q5.2, R6.1, R10.2, R15.1, TP10.1, U10.16, U11.16, U18.3, U19.3, VR1.3
/9V: C2.1, C4.1, C9.1, JP3.2, Q24.2, R7.1, R11.2, R54.1, TP11.1, U6.12
/Connectors/DIO_IN_BRIDGE: U14.10, U15.9
/Connectors/DIO_SS: Q22.3, R47.2, U14.1, U15.1
/Connectors/LDR_EN: CN21.10, U13.1
/Connectors/LDR_ID0: CN21.4, R48.2, U15.13
/Connectors/LDR_ID1: CN21.5, R49.2, U15.14
/Connectors/LDR_ID2: CN21.6, R50.2, U15.3
/Connectors/LDR_SPIN: CN21.9, U13.15
/Connectors/SIG1: CN22.3, U14.11
/Connectors/SIG2: CN23.3, U14.12
/Connectors/SIG3: CN24.3, U14.13
/Connectors/SIG4: CN25.3, U14.14
/Connectors/SIG5: CN26.3, U14.3
/Connectors/SIG6: CN27.3, U14.4
/Connectors/SIG7: CN28.3, U14.5
/Connectors/SIG8: CN29.3, U14.6
/DIO_MISO: CN20.1150, U14.9
/DIO_MOSI: CN20.1162, U9.14
/DIO_SCK: CN20.1146, U9.11, U13.11, U14.2, U15.2
/ECHO1: CN9.3, CN20.1104
/ECHO2: CN10.3, CN20.1156
/ECHO3: CN11.3, CN20.1247
/ECHO4: CN12.3, CN20.1249
/ECHO5: CN14.3, CN20.1251
/ECHO6: CN16.3, CN20.1253
/ECHO7: CN19.3, CN20.1240
/ESTOP_CLR: CN20.1140, U20.1
/GND: BT1.2, C1.2, C2.2, C3.2, C4.2, C5.2, C6.2, C7.2, C8.1, C9.2, C10.2, C11.2, C12.2, C13.2, C14.2, C15.2, C16.2, C17.2, C18.2, C19.2, C20.1, C21.1, C22.1, C23.1, CN1.A1, CN1.A12, CN1.B1, CN1.B12, CN2.A1, CN2.A12, CN2.B1, CN2.B12, CN3.2, CN3.3, CN3.6, CN3.7, CN4.2, CN5.6, CN5.9, CN5.14, CN5.20, CN5.25, CN5.30, CN5.34, CN5.39, CN6.4, CN7.4, CN8.3, CN9.4, CN10.4, CN11.4, CN12.4, CN14.4, CN16.4, CN19.4, CN20.1108, CN20.1119, CN20.1120, CN20.1122, CN20.1149, CN20.1160, CN20.1209, CN20.1220, CN20.1232, CN20.1239, CN20.1254, CN20.1263, CN21.3, CN22.1, CN23.1, CN24.1, CN25.1, CN26.1, CN27.1, CN28.1, CN29.1, CN30.3, CN30.4, CN30.9, CN30.10, D5.1, D22.1, JP1.2, JP7.2, JP8.3, JP9.2, Q4.2, Q22.2, Q23.2, Q25.2, R1.1, R2.1, R3.1, R4.1, R14.2, R16.2, R18.2, R25.1, R26.1, R46.2, R51.2, SW2.1, TP2.1, TP3.1, TP4.1, TP5.1, TP6.1, TP8.1, U1.2, U1.3, U2.2, U2.3, U3.2, U3.3, U4.4, U5.1, U5.2, U5.3, U5.4, U6.13, U6.17, U7.8, U7.13, U8.8, U8.13, U9.8, U9.13, U10.8, U10.13, U11.8, U11.13, U12.3, U12.4, U12.5, U13.8, U13.13, U14.8, U14.15, U15.8, U15.10, U15.11, U15.12, U15.15, U16.2, U17.2, U18.2, U19.2, U20.4, U21.2, U22.1, VR1.1
/LDR_PWM: CN20.1241, CN21.11
/LDR_RX: CN20.1230, CN21.8
/LDR_TX: CN20.1216, CN21.7
/LED's/LED1: Q21.1, U8.15
/LED's/LED2: Q19.1, U8.1
/LED's/LED3: Q17.1, U8.2
/LED's/LED4: Q15.1, U8.3
/LED's/LED5: Q13.1, U8.4
/LED's/LED6: Q11.1, U8.5
/LED's/LED7: Q9.1, U8.6
/LED's/LED8: Q7.1, U8.7
/LED's/LED8_SER: U7.14, U8.9
/LED's/LED9: Q20.1, U7.15
/LED's/LED10: Q18.1, U7.1
/LED's/LED11: Q16.1, U7.2
/LED's/LED12: Q14.1, U7.3
/LED's/LED13: Q12.1, U7.4
/LED's/LED14: Q10.1, U7.5
/LED's/LED15: Q8.1, U7.6
/LED's/LED16: Q6.1, U7.7
/LED's/LEDS_GND: JP8.2, Q6.2, Q7.2, Q8.2, Q9.2, Q10.2, Q11.2, Q12.2, Q13.2, Q14.2, Q15.2, Q16.2, Q17.2, Q18.2, Q19.2, Q20.2, Q21.2
/LEDS_MOSI: CN20.1222, U8.14
/LEDS_SCLK: CN20.1101, U7.11, U8.11
/LMOTOR_CTL1: CN20.1227, U6.16
/LMOTOR_CTL2: CN20.1229, U6.15
/LQUAD_A: CN6.5, CN20.1243
/LQUAD_B: CN6.6, CN20.1132, CN20.1161
/Motors_Encoders/BMOTOR_OUT1: CN7.2, U6.7
/Motors_Encoders/BMOTOR_OUT2: CN7.1, U6.5
/Motors_Encoders/BMOTOR_SEN: R26.2, U6.6
/Motors_Encoders/LMOTOR_OUT1: CN6.1, U6.2
/Motors_Encoders/LMOTOR_OUT2: CN6.2, U6.4
/Motors_Encoders/LMOTOR_SEN: R25.2, U6.3
/P5V: C3.1, CN13.2, CN15.2, CN17.2, CN18.2, JP5.2, R8.1, R9.2, R27.1, R28.1, R29.1, R30.1, R31.1, R32.1, R33.1, R34.1, R35.1, R36.1, R37.1, R38.1, R39.1, R40.1, R41.1, R42.1, TP9.1
/Power/3.3V_LED: D1.2, R5.2
/Power/5V_LED: D2.2, R6.2
/Power/9V_LED: D3.2, R7.2
/Power/CN1_5V: CN1.A4, CN1.A9, CN1.B4, CN1.B9, Q1.3, TP1.1, U1.1, U1.4
/Power/CN2_5V: CN2.A4, CN2.A9, CN2.B4, CN2.B9, Q2.3, U2.1, U2.4
/Power/GATE1: Q1.1, U1.5
/Power/GATE2: Q2.1, U2.5
/Power/GATE3: Q3.1, U3.5
/Power/P5V_LED: D4.2, R8.2
/Power/SHUNT_3.3: C1.1, JP4.1, R12.1, VR1.2
/Power/SHUNT_5V: JP2.1, Q1.2, Q2.2, Q3.3, R10.1, U1.6, U2.6, U3.1, U3.4
/Power/SHUNT_9V: CN3.8, CN3.9, JP3.1, R11.1
/Power/SHUNT_P5V: JP5.1, Q3.2, R9.1, U3.6
/RMOTOR_CTL1: CN20.1202, U6.9
/RMOTOR_CTL2: CN20.1224, U6.10
/RQUAD_A: CN7.5, CN20.1204
/RQUAD_B: CN7.6, CN20.1219
/SBC_ALIVE: CN5.24, CN20.1157, R18.1, R20.1
/SERVO1: CN20.1128, U10.9
/SERVO2: CN20.1231, U10.7
/SERVO3: CN20.1225, U10.5
/SERVO4: CN20.1218, U10.3
/SERVO_CUR: C16.1, CN20.1135, R44.1
/SERVO_POS: CN20.1154, R45.2, R46.1
/SER_IO: U9.9, U13.14
/SPBC_RX: CN5.10, CN20.1217, TP13.1
/SPBC_TX: CN5.8, CN20.1226, TP12.1
/STL_RX: CN8.7, CN20.1210
/STL_TX: CN8.8, CN20.1169
/SWCLK: CN8.2, CN20.1115
/SWDIO: CN8.4, CN20.1113
/Single Board Computer/ID_SCL: CN5.28, R23.2, U5.6
/Single Board Computer/ID_SDA: CN5.27, R22.2, U5.5
/Single Board Computer/RPI_DSP_EN: CN5.11, JP6.2, Q4.1
/Single Board Computer/SBC_REQ: R17.1, SW1.1
/Single Board Computer/SBC_SCL: CN5.5, R21.2, U4.6
/Single Board Computer/SBC_SDA: CN5.3, R19.2, U4.5
/Single Board Computer/SBC_STOP: CN5.23, R16.1, R17.2
/Single Board Computer/VBAT: BT1.1, U4.3
/Single Board Computer/WP: JP7.1, R24.2, U5.7
/Single Board Computer/X1: C7.1, U4.1, X1.2
/Single Board Computer/X2: C5.1, U4.2, X1.1
/Sonars and Servos/SERVO1_5V: CN18.3, U10.10
/Sonars and Servos/SERVO2_5V: CN17.3, U10.6
/Sonars and Servos/SERVO3_5V: CN15.3, U10.4
/Sonars and Servos/SERVO4_5V: CN13.3, U10.2
/Sonars and Servos/SGND: CN13.1, CN15.1, CN17.1, CN18.1, U12.1, U12.2
/Sonars and Servos/TRIG1: U9.15, U11.3
/Sonars and Servos/TRIG1_5V: CN9.2, U11.2
/Sonars and Servos/TRIG2: U9.1, U11.5
/Sonars and Servos/TRIG2_5V: CN10.2, U11.4
/Sonars and Servos/TRIG3: U9.2, U11.7
/Sonars and Servos/TRIG3_5V: CN11.2, U11.6
/Sonars and Servos/TRIG4: U9.3, U11.9
/Sonars and Servos/TRIG4_5V: CN12.2, U11.10
/Sonars and Servos/TRIG5: U9.4, U11.11
/Sonars and Servos/TRIG5_5V: CN14.2, U11.12
/Sonars and Servos/TRIG6: U9.5, U11.14
/Sonars and Servos/TRIG6_5V: CN16.2, U11.15
/Sonars and Servos/TRIG7: U9.6, U10.14
/Sonars and Servos/TRIG7_5V: CN19.2, U10.15
/WOWBus/WOW_COMH: CN30.6, U18.7, U21.3
/WOWBus/WOW_COML: CN30.5, R58.2, U18.6
/WOWBus/WOW_COM_OPTO: R60.1, U21.1
/WOWBus/WOW_ESTOP_OPTO: R61.2, U22.2
/WOWBus/WOW_POW_OUT: CN30.1, CN30.2, CN30.11, CN30.12, JP10.2, R56.2
/WOWBus/WOW_STDBY: Q25.3, R55.2, U18.8, U19.8
/WOWBus/WOW_STOPH: CN30.7, U19.7, U22.3
/WOWBus/WOW_STOPL: CN30.8, R59.2, U19.6
/WOWBus/~NESTOP_SET: TP16.1, U17.4, U20.6
/WOWBus/~NHR2_ESTOP: U16.6, U19.4, U20.3
/WOWBus/~NWOW_EN: Q23.3, Q24.1, R54.2
/WOW_EN: CN20.1103, Q23.1, Q25.1, R51.1, R60.2, R61.1
/WOW_RX: CN20.1141, TP15.1, U18.4
/WOW_TX: CN20.1143, TP14.1, U18.1
/~DIO_NSS: CN20.1148, Q22.1, U9.12, U13.12
/~LEDS_NSS: CN20.1117, U7.12, U8.12
/~NBTN_ESTOP: JP9.1, R53.2, SW2.2, U15.5, U17.6
/~NESTOP: CN5.40, CN20.1145, R57.1, U6.1, U16.4
/~NMOTOR_FAULT: R52.2, U6.8, U15.4, U17.1
/~NRST: CN8.5, CN20.1114, U7.10, U8.10, U9.10, U13.10, U17.3
/~NWOW_ESTOP: TP17.1, U15.6, U16.3, U19.1
unnamed: C10.1, U6.14
unnamed: CN1.A5, R3.2
unnamed: CN1.B5, R4.2
unnamed: CN2.A5, R1.2
unnamed: CN2.B5, R2.2
unnamed: CN4.1, Q5.3
unnamed: CN18.4, R45.1
unnamed: CN20.1137, CN20.1201
unnamed: CN20.1223, CN20.1242
unnamed: D1.1, D2.1, D3.1, D4.1, JP1.1
unnamed: D5.2, R20.2
unnamed: D6.1, Q6.3
unnamed: D6.2, R27.2
unnamed: D7.1, Q7.3
unnamed: D7.2, R28.2
unnamed: D8.1, Q8.3
unnamed: D8.2, R29.2
unnamed: D9.1, Q9.3
unnamed: D9.2, R30.2
unnamed: D10.1, Q10.3
unnamed: D10.2, R31.2
unnamed: D11.1, Q11.3
unnamed: D11.2, R32.2
unnamed: D12.1, Q12.3
unnamed: D12.2, R33.2
unnamed: D13.1, Q13.3
unnamed: D13.2, R34.2
unnamed: D14.1, Q14.3
unnamed: D14.2, R35.2
unnamed: D15.1, Q15.3
unnamed: D15.2, R36.2
unnamed: D16.1, Q16.3
unnamed: D16.2, R37.2
unnamed: D17.1, Q17.3
unnamed: D17.2, R38.2
unnamed: D18.1, Q18.3
unnamed: D18.2, R39.2
unnamed: D19.1, Q19.3
unnamed: D19.2, R40.2
unnamed: D20.1, Q20.3
unnamed: D20.2, R41.2
unnamed: D21.1, Q21.3
unnamed: D21.2, R42.2
unnamed: D22.2, R57.2
unnamed: JP6.1, R14.1
unnamed: JP6.3, R13.2
unnamed: JP10.1, Q24.3, R56.1
unnamed: Q4.3, Q5.1, R15.2
unnamed: R43.2, U12.6
unnamed: R44.2, U12.7
unnamed: R58.1, U21.4
unnamed: R59.1, U22.4

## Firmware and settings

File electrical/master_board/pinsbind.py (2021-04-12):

# MIT License
#
# Copyright 2020 Home Brew Robotics Club
#
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
# <--------------------------------------- 100 characters ---------------------------------------> #

# This program is run using the corresponding `Makefile` which does the following:
#
#        mypy pins_bind.py                           # Do static type checking
#        flake8 --max-line-length=100 pins_bind.py   # Search for misc. errors (unsed variables,...)
#        pydocstyle pins_bind.py                     # Make sure the doc strings are consistent.
#        python pins_bind.py                         # Run the program
#
# Note: that this file is formated to stay with 100 characters as enforced by flake8.

"""Figure out pin binding for Morpho/Zio connectors."""

# Use type hints for mypy program.
import csv  # .csv file parser (CSV => Comma Separated Values)
import itertools
from typing import Dict, IO, List, Set, Text, Tuple

# Some type definitions:

# An ANNOTATED_PIN_NAME has the form ".P[A-F][0-9]+:AF[0-9]+" (using regular expression format).
# The first character is '@' for an Arduino pin, '+' for a daughter pin (i.e. a Zio pin that
# that is not an Arduino pin), and '-' for a Morpho pin that is not connected to the Zio connectors.
# There is a single letter after the 'P' that is the a port name (e.g. 'PA' - 'PF').
# Lastly there is an alternate function designator which is 'AF' followed by by a number between
# 0 and 14.  For example "@PD14:AF11" is an arduino ('@') pin connected to pin name 'PD14',
# using alternate function "AF11".

# Define TextTuple as an abreviation.  In general, Tuples are needed to support Python sorting.
TextTuple = Tuple[Text, ...]  # Helper type to make the code easier to read.

# A Binding is a ("SIGNAL_NAME", "ANNOTATED_PIN_NAME", "SCHEMATIC_NAME") tuple.
Binding = Tuple[Text, Text, Text]
Row = TextTuple  # A helper type for a row read from a `.csv` file.

# A Signal is a ("SIGNAL_NAME", "ANNOTATED_PIN_NAME1", ..., "ANNOTATED_PIN_NAMEn")
# There is always a signal name and 0, 1 or more annotated pin names.
Signal = TextTuple
Signals = Tuple[TextTuple, ...]  # Signal lists are organized a tuple of text tuples.

# A PinBind represnt a request to bind an internal signal to a schematics symbol with contraints
# using the following tuple format:
#    ("SIGNAL_NAME", "SCHEMATIC_NAME", SIGNALS, "FORCE_PIN_NAME")
# where,
#    "SIGNAL_NAME" is the internal signal name.
#    "SCHEMATIC_NAME" is the schemtatic name.
#    "SIGNALS" is one of the signals subset (e.g. Arduino, Daughter, or Morpho)
#    "FORCE_PIN_NAME" When non-empty, force a signal binding to a specific pin.
#                     The same signal can be bound to more that one pin using this feature.
PinBind = Tuple[Text, Text, Signals, Text]


def main() -> None:
    """Figure out pin binding for Morpho/ZIO connectors."""
    # Extract the Arduino/Daughter/Morpho Signals/Sets.  See the README.md for what these
    # 3 sets are all about:
    arduino_signals: Signals
    daughter_signals: Signals
    morpho_signals: Signals
    arduino_set: Set[Text]
    daughter_set: Set[Text]
    morpho_set: Set[Text]
    pin_numbers_table: Dict[Text, int]
    arduino_signals, daughter_signals, morpho_signals, \
        arduino_set, daughter_set, morpho_set, pin_numbers_table = pin_signals_sets_get()

    # Create *periperal_permutations* list that lists all the possible permutations of
    # each peripheral class.  The number of I2C's, SPI's, and UART's are specified:
    i2cs_want: int = 1  # One manaully pre-bound to Arduino and one for everything else.
    spis_want: int = 2  # + SPI1 is already bound to Arduino
    uarts_want: int = 5  # + UART6 is already bound to Arduino
    peripheral_permutations: Tuple[TextTuple, ...] = peripheral_permutations_get(
        i2cs_want, spis_want, uarts_want)
    print(f"len(peripheral_permutations)={len(peripheral_permutations)}")

    # Iterate across *peripheral_permutations* searching for the solutions with no unbound signal
    # names.  The *permutation_scores* list shows the results of the search and can be sorted to
    # find solutions with the fewest (hopefully 0) unbound pins.  A *permutation_score* has the
    # format of (len(unbounded_signals), unbounded_signals, permutation):
    permutation_scores: List[Tuple[int, TextTuple, TextTuple]] = []
    peripheral_permutation: TextTuple
    for peripheral_permutation in peripheral_permutations:
        # Create the *pin_binds* list from a single *peripheral_permuatation*.
        pin_binds: List[PinBind] = pin_binds_get(peripheral_permutation, arduino_signals,
                                                 daughter_signals, morpho_signals)

        # Perform the pin bindings.  Ignore the the resulting pin/signals tables, but keep
        # the *unbound_signals* and build up a *permutation_score*:
        signal_bindings_table: Dict[Text, Tuple[Binding, ...]]
        pin_bindings_table: Dict[Text, Binding]
        unbound_signals: TextTuple
        signal_bindings_table, pin_bindings_table, unbound_signals = pins_bind(pin_binds)
        permutation_score: Tuple[int, TextTuple, TextTuple] = (
            len(unbound_signals),
            tuple(unbound_signals),
            peripheral_permutation,
        )
        permutation_scores.append(permutation_score)

    # Sort *permutation_scores* so that the best permutations sort to the front:
    permutation_scores = sorted(permutation_scores)

    # Now unpack the first entry in *permutation scores* to select one that has the lowest
    # number of unbound signals:
    initial_unbound_signals_size: int
    permutation: TextTuple
    initial_unbound_signals_size, unbound_signals, permutation = permutation_scores[0]
    if initial_unbound_signals_size == 0:
        # We have a winner, so we can show a more detailed summary of the solution:
        summary_show(permutation,
                     arduino_signals, daughter_signals, morpho_signals,
                     arduino_set, daughter_set, morpho_set, pin_numbers_table)
    else:
        # Nope, we are asking for too much and ran out of pins.  So now we list all of the
        # permutations that have the same number of unbound signals as the first one.
        permutation_record: Tuple[int, TextTuple, TextTuple]
        print("Unbound siginals:")
        unbound_signals_size: int
        for unbound_signals_size, unbound_signals, permutation in permutation_scores:
            if unbound_signals_size > initial_unbound_signals_size:
                # We do not need to look as solutions that event more unbound signals than
                # the first one.
                break
            print(f"{unbound_signals}: {permutation}")
        print("")


# The functions after main() are listed alphabetically to make them easier to find.

def all_signals_extract(zios_table: Dict[Text, Text]) -> Tuple[Tuple[Signal, ...], Dict[Text, int]]:
    """Return the extracted signals as a sorted tuple.

    The signals table maps an internal signals table to tuple of the form:

        ("SIGNAL_NAME", "ANNOTATED_PIN1", ..., "ANNOTATED_PINn")

    where,
        "SIGNAL_NAME" is the internal signal name used by the processor
            spec. sheet.
        "ANNOTATEDPINi" is an annotated PIN of the form:
            "{FLAG}{PIN_NAME}:{ALTERNATE_FUNCTION_NAME}"
        where,
            {FLAG} is:
                '@' pin is an Arduino pin (by definition a Zio pin)
                '+' pin is a Zio Pin, but not an Arduino pin
                '-' pin is a Morpho pin, but not a Zio pin
            {PIN_NAME} is "P{PORT_LETTER}{PIN_NUMBER}:
                PORT_LETTER is a letter between 'A'and 'G'.
                PIN_NUMBER is a letter between 0 and 15.
            {ALTERNATE_FUNCTION_NAME} is "AF" follow by a number between 0 and 14.
    """
    # Read in the alternate functions table from the .csv file for the Nucleo144-767ZI:
    headings: Row
    data_rows: Tuple[Row, ...]
    headings, data_rows = alternate_functions_csv_read()

    # Find *pin_number_index*, *pin_name_index* and *af_indices* from the *headings*:
    heading: Text
    pin_number_index: int = -1
    pin_name_index: int = -1
    af_indices: Dict[int, int] = {}
    index: int
    for index, heading in enumerate(headings):
        # print(f"Heading[{index}]:'{heading}'")
        if heading == "Position":
            pin_number_index = index
        elif heading == "Name":
            pin_name_index = index
        elif heading.startswith("AF") and heading[2:].isdigit():
            af_number: int = int(heading[2:])
            # print(f"af_number:{af_number}")
            af_indices[af_number] = index
    assert pin_name_index >= 0
    assert pin_number_index >= 0
    assert len(af_indices) == 15

    # Now scan through the *data_rows* building up useful tables.  The *pins_table* builds
    # up information about signals that can be connected to a given pin name.
    # The *signals_table* builds up a list of pin names that can be connected to each signal.
    pins_table: Dict[Text, TextTuple] = {}
    pin_numbers_table: Dict[Text, int] = {}
    signals_table: Dict[Text, List[Text]] = {}

    # Some shared variables used both inside and outside of the loops:
    signal_pins: List[Text]
    data_row: Row
    signal_name: Text
    af0_index: int = af_indices[0]
    # print(f"af0_index={af0_index}")

    # Iterate over *data_rows*:
    data_row_index: int
    for data_row_index, data_row in enumerate(data_rows):
        # Grab the *pin_number*
        pin_number: int
        try:
            pin_number = int(data_row[pin_number_index])
        except ValueError:
            assert False, "Bad pin number"

        # Grab the *pin_name* and only look at pins of the form "P[A-G]#", where '#" is a number.
        pin_name: Text = data_row[pin_name_index]
        pin_name_fields: List[Text] = pin_name.split('/')
        if len(pin_name_fields) >= 1:
            pin_name = pin_name_fields[0]
        if (
                len(pin_name) >= 3 and pin_name[0] == 'P' and
                pin_name[1] in "ABCDEFGH" and pin_name[2:].isdigit()):
            # print(f"Pin[{pin_number}]:'{pin_name}'")
            pin_numbers_table[pin_name] = pin_number

            # The altenate data function bundings are at the end starting at *af0_index*.
            # Their should be 15 of them.
            afs: TextTuple = data_row[af0_index:]
            assert len(afs) == 15
            pins_table[pin_name] = afs

            # Now fill in the *signals_table*:
            af_index: int
            signal_names: Text
            for af_index, signal_names in enumerate(afs):
                # For now ignore signals that are not needed by HR2 right now:
                for signal_name in signal_names.split('/'):
                    # Ignore uninteresting signals that will not be bound to:
                    if signal_name and not signal_name_ignore(signal_name):
                        # Ensure *signal_name* is in *signals_table* and get *signal_pins* list:
                        if signal_name not in signals_table:
                            signals_table[signal_name] = [signal_name]
                        signal_pins = signals_table[signal_name]

                        # Only keep track of pins that are "free" for use on the ZIO connectors:
                        # The *zios_table* has a '@', '+', '-' for Arduino/Daughter/Morpho.
                        zios_flag: Text = zios_table[pin_name]
                        if zios_flag in "+@-":
                            annotated_pin: Text = f"{zios_flag}{pin_name}:AF{af_index}"
                            signal_pins.append(annotated_pin)
                        # print(f"  '{signal_name}':{signal_pins}")

    # Create the *signals_stuple* list from the *signals_table*, using tuples instead of lists.
    # It is really important that the *signals* be a Tuple so it can be used as a dictionary key
    # later on in the program:
    signals: List[Signal] = []
    for signal_pins in signals_table.values():
        signals.append(tuple(signal_pins))
    signals_tuple: Tuple[Signal, ...] = tuple(sorted(signals))

    # For reference/debugging perposes, write *signals_tuple* out to `/tmp/signals.txt`:
    signals_file: IO[Text]
    with open("/tmp/signals.txt", "w") as signals_file:
        for signal in signals_tuple:
            signals_file.write(f"{str(signal)}\n")
    return signals_tuple, pin_numbers_table


def alternate_functions_csv_read() -> Tuple[Row, Tuple[Row, ...]]:
    """Read the alternate functions table."""
    # Read in *rows* from "stm32f7676_af.csv" file:
    rows: List[TextTuple] = []
    csv_file: IO[Text]
    with open("stm32f767_af.csv", "r") as csv_file:
        af_reader = csv.reader(csv_file, delimiter=',', quotechar='"')
        for row_list in af_reader:
            rows.append(tuple(row_list))

    # The first row is the column *headings* and the remaining rows are the *data_rows*:
    headings: Row = rows[0]
    data_rows: Tuple[Row, ...] = tuple(rows[1:])
    return headings, data_rows


def morpho_set_extract() -> Set[Text]:
    """Return the Morph pin names read from .csv file."""
    # Read in *rows* from "morpho_.csv" file:
    rows: List[TextTuple] = []
    csv_file: IO[Text]
    with open("morpho_pins.csv", "r") as csv_file:
        af_reader = csv.reader(csv_file, delimiter=',', quotechar='"')
        for row_list in af_reader:
            rows.append(tuple(row_list))

    # The first row is the column *headings* and the remaining rows are the *data_rows*:
    data_rows: Tuple[Row, ...] = tuple(rows[1:])

    morpho_set: Set[Text] = set()
    data_row: TextTuple
    for data_row in data_rows:
        if len(data_row) >= 4:
            pin_name = data_row[2]
            if pin_name.startswith('@'):
                pin_name = pin_name[1:]
            if (
                    len(pin_name) >= 3 and pin_name[0] == 'P' and
                    pin_name[1] in "ABCDEFG" and pin_name[2:].isdigit()):
                morpho_set |= set(pin_name)
    return morpho_set


def nucleo_set_create() -> Set[Text]:
    """Return the processor pins used by the Nucleo-144."""
    pin_number_name_uses: List[Tuple[int, Text, Text]] = [
        (7, "PC13", "USER_Btn"),
        (8, "PC14", "RCC_OSC32_IN"),
        (9, "PC15", "RCC_OSC32_OUT"),
        (23, "PH0", "OSC_IN"),
        (24, "PH1", "OSC_OUT"),
        (27, "PC1", "RMII_MDC"),
        (35, "PA1", "RMII_REF_CLK"),
        (36, "PA2", "RMII_MDIO"),
        (43, "PA7", "RMII_CRS_DV"),  # ZIO overlap @D11
        (44, "PC4", "RMII_RXD0"),
        (45, "PC5", "RMII_RXD1"),
        (46, "PB0", "LD1"),  # ZIO overlap CN10-31
        (91, "PG6", "USB_PowerSwitchOn"),
        (92, "PG7", "USB_OverCurrent"),
        (100, "PA8", "USB_SOF"),
        (101, "PA9", "USB_VBUS"),
        (102, "PA10", "USB_ID"),
        (103, "PA11", "USB_DM"),
        (104, "PA12", "USB_DP"),
        (105, "PA13", "TMS"),
        (109, "PA14", "TCK"),
        (126, "PG11", "RMII_TX_EN"),
        (128, "PG13", "RMII_TXD0"),
        (133, "PB3", "SWO"),  # CN7-15
        (137, "PB7", "LD2 (Blue)"),  # Correct
    ]
    pin_number_name_use: Tuple[int, Text, Text]
    nucleo_set: Set[Text] = {pin_number_name_use[1]
                             for pin_number_name_use in pin_number_name_uses}
    return nucleo_set


def ordered_permutations(peripherals: TextTuple, count: int) -> TextTuple:
    """Return a sorted list of unique permutations."""
    # The output of the *permutations*() is an unordered list of permutations.
    # Sort them and stuff them into a set to to cull duplicates.
    permuation: List[Text]
    permutations_set: Set[Text] = set()
    for permutation in itertools.permutations(peripherals, count):
        sorted_permutation: Text = ':'.join(sorted(permutation))
        permutations_set.add(sorted_permutation)

    # Extract the final *ordered_permutations* from the set and return them:
    ordered_permutations: TextTuple = tuple(sorted(permutations_set))
    return ordered_permutations


def peripheral_permutations_get(
        i2cs_count: int, spis_count: int, uarts_count: int) -> Tuple[TextTuple, ...]:
    """Return permuation list for I2C, SPI, and UART peripherals."""
    # These are the list of peripherals to permuate:
    i2cs: TextTuple = ("I2C1", "I2C2", "I2C4")  # "I2C3" is manually shorted to arduino pins
    spis: TextTuple = ("SPI2", "SPI3", "SPI4", "SPI5", "SPI6")  # SPI1 is prebound to arduino.
    # UART6 is already connected to Arduino pins already
    # UART8 Conflicts with LPTIM_IN1 on PE1 and there is no work around.  UART8 is not avaiable.
    uarts: TextTuple = ("USART1", "USART2", "USART3", "USART4", "UART5", "UART7")

    # Create the permutations for the I2C's, SPI'2, and UART's:
    i2c_permutations: TextTuple = ordered_permutations(i2cs, i2cs_count)
    spi_permutations: TextTuple = ordered_permutations(spis, spis_count)
    uart_permutations: TextTuple = ordered_permutations(uarts, uarts_count)

    # Just iterate over all possible permutations of each peripheral type:
    peripheral_permutations: List[TextTuple] = []
    i2c_permutation: Text
    for i2c_permutation in i2c_permutations:
        spi_permutation: Text
        for spi_permutation in spi_permutations:
            uart_permutation: Text
            for uart_permutation in uart_permutations:
                # Join all three permutaions into a single *peripheral_permutation:
                peripheral_permutation: TextTuple = tuple(sorted(
                    uart_permutation.split(':') +
                    i2c_permutation.split(':') +
                    spi_permutation.split(':')
                ))
                # print(f"Peripheral Permutation: {peripheral_permutation}")
                peripheral_permutations.append(peripheral_permutation)
    return tuple(peripheral_permutations)
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

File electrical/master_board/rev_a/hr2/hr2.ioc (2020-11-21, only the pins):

Mcu.UserName=STM32F767ZITx
PA0/WKUP.GPIO_Label=SERVO1
PA0/WKUP.Signal=GPIO_Output
PA1.GPIO_Label=RMII_REF_CLK [LAN8742A-CZ-TR_REFCLK0]
PA1.Signal=ETH_REF_CLK
PA10.GPIO_Label=USB_ID
PA10.Signal=USB_OTG_FS_ID
PA11.GPIO_Label=USB_DM
PA11.Signal=USB_OTG_FS_DM
PA12.GPIO_Label=USB_DP
PA12.Signal=USB_OTG_FS_DP
PA13.GPIO_Label=SWDIO
PA13.Signal=SYS_JTMS-SWDIO
PA14.GPIO_Label=SWCLK
PA14.Signal=SYS_JTCK-SWCLK
PA15.GPIO_Label=LEDS_NSS
PA15.Signal=SPI3_NSS
PA2.GPIO_Label=RMII_MDIO [LAN8742A-CZ-TR_MDIO]
PA2.Signal=ETH_MDIO
PA3.GPIO_Label=A0
PA3.Signal=ADCx_IN3
PA4.GPIO_Label=LQUAD_B
PA4.Signal=GPIO_Input
PA5.GPIO_Label=D13_SCK
PA5.Signal=SPI1_SCK
PA6.GPIO_Label=D12_MISO
PA6.Signal=SPI1_MISO
PA7.GPIO_Label=D11_PWM_MOSI
PA7.Signal=SPI1_MOSI
PA8.Signal=I2C3_SCL
PA9.GPIO_Label=USB_VBUS`
PA9.Signal=USB_OTG_FS_VBUS
PB0.GPIO_Label=GRN_LED
PB0.Signal=GPIO_Output
PB1.GPIO_Label=RMOTOR_CTL2
PB1.Signal=S_TIM3_CH4
PB10.GPIO_Label=SERVO3
PB10.Signal=S_TIM2_CH3
PB11.GPIO_Label=SERVO4
PB11.Signal=S_TIM2_CH4
PB12.GPIO_Label=LIDAR_TX
PB12.Signal=UART5_RX
PB13.GPIO_Label=LIDAR_RX
PB13.Signal=UART5_TX
PB14.GPIO_Label=LD3 [Red]
PB14.Signal=GPIO_Output
PB15.GPIO_Label=SBC_TX
PB15.Signal=USART1_RX
PB2.GPIO_Label=LEDS_MOSI
PB2.Signal=SPI3_MOSI
PB3.GPIO_Label=SERVO2
PB3.Signal=S_TIM2_CH2
PB4.GPIO_Label=LMOTOR_CTL1
PB4.Signal=S_TIM3_CH1
PB5.GPIO_Label=LMOTOR_CTL2
PB5.Signal=S_TIM3_CH2
PB6.GPIO_Label=SBC_RX
PB6.Signal=USART1_TX
PB7.GPIO_Label=BLUE_LED
PB7.Signal=GPIO_Output
PB8.GPIO_Label=D15
PB8.Signal=GPIO_Input
PB9.GPIO_Label=D14
PB9.Signal=GPIO_Input
PC0.GPIO_Label=A1
PC0.Signal=ADCx_IN10
PC1.GPIO_Label=RMII_MDC [LAN8742A-CZ-TR_MDC]
PC1.Signal=ETH_MDC
PC10.GPIO_Label=LEDS_SCK
PC10.Signal=SPI3_SCK
PC11.GPIO_Label=LEDS_MISO
PC11.Signal=SPI3_MISO
PC12.GPIO_Label=WOW_EN
PC12.Signal=GPIO_Output
PC13.GPIO_Label=USER_BTN
PC13.Signal=GPXTI13
PC14/OSC32_IN.Signal=RCC_OSC32_IN
PC15/OSC32_OUT.Signal=RCC_OSC32_OUT
PC2.GPIO_Label=SERVO_CUR
PC2.Signal=ADCx_IN12
PC3.GPIO_Label=A2
PC3.Signal=ADCx_IN13
PC4.GPIO_Label=RMII_RXD0 [LAN8742A-CZ-TR_RXD0]
PC4.Signal=ETH_RXD0
PC5.GPIO_Label=RMII_RXD1 [LAN8742A-CZ-TR_RXD1]
PC5.Signal=ETH_RXD1
PC6.GPIO_Label=RQUAD_A
PC6.Signal=S_TIM8_CH1
PC7.GPIO_Label=RQUAD_B
PC7.Signal=S_TIM8_CH2
PC8.GPIO_Label=RMOTOR_CTL1
PC8.Signal=S_TIM3_CH3
PC9.GPIO_Label=A4_SDA
PC9.Signal=I2C3_SDA
PD0.GPIO_Label=SBC_ALIVE
PD0.Signal=GPIO_Output
PD1.GPIO_Label=INT1
PD1.Signal=GPXTI1
PD12.GPIO_Label=LQUAD_A
PD12.Signal=LPTIM1_IN1
PD13.GPIO_Label=LIDAR_PWM
PD13.Signal=S_TIM4_CH2
PD14.GPIO_Label=D10_PWM_NSS
PD14.Signal=S_TIM4_CH3
PD15.GPIO_Label=D9_PWM
PD15.Signal=S_TIM4_CH4
PD2.GPIO_Label=ECHO1
PD2.Signal=GPXTI2
PD3.GPIO_Label=ESTOP_CLR
PD3.Signal=GPIO_Output
PD5.GPIO_Label=WOW_RX
PD5.Signal=USART2_TX
PD6.GPIO_Label=WOW_TX
PD6.Signal=USART2_RX
PD7.GPIO_Label=ESTOP
PD7.Signal=GPXTI7
PD8.GPIO_Label=STL_RX
PD8.Signal=USART3_TX
PD9.GPIO_Label=STL_TX
PD9.Signal=USART3_RX
PE0.GPIO_Label=INT0
PE0.Signal=GPIO_Input
PE1.GPIO_Label=LQUAD_B
PE1.Signal=LPTIM1_IN2
PE10.GPIO_Label=ECHO3
PE10.Signal=GPIO_Input
PE11.GPIO_Label=D5_PWM
PE11.Signal=S_TIM1_CH2
PE12.GPIO_Label=ECHO4
PE12.Signal=GPIO_Input
PE13.GPIO_Label=D3_PWM
PE13.Signal=S_TIM1_CH3
PE14.GPIO_Label=ECHO5
PE14.Signal=GPIO_Input
PE15.GPIO_Label=ECHO6
PE15.Signal=GPIO_Input
PE2.GPIO_Label=DIO_SCK
PE2.Signal=SPI4_SCK
PE4.GPIO_Label=DIO_NSS
PE4.Signal=SPI4_NSS
PE5.GPIO_Label=DIO_MOSO
PE5.Signal=SPI4_MISO
PE6.GPIO_Label=DIO_MOSI
PE6.Signal=SPI4_MOSI
PE7.GPIO_Label=FPGA_TX
PE7.Signal=UART7_RX
PE8.GPIO_Label=ECHO7
PE8.Signal=GPIO_Input
PE9.GPIO_Label=D6_PWM
PE9.Signal=S_TIM1_CH1
PF0.GPIO_Label=MISC_SDA
PF0.Signal=I2C2_SDA
PF1.GPIO_Label=MISC_SCL
PF1.Signal=I2C2_SCL
PF10.GPIO_Label=A5_SCL
PF10.Signal=ADC3_IN8
PF3.GPIO_Label=A3
PF3.Signal=ADC3_IN9
PF5.GPIO_Label=A4_SDA
PF5.Signal=ADC3_IN15
PF7.GPIO_Label=FPGA_RX
PF7.Signal=UART7_TX
PF8.GPIO_Label=SERVO_POS
PF8.Signal=ADC3_IN6
PF9.GPIO_Label=ECHO2
PF9.Signal=GPIO_Input
PG11.GPIO_Label=RMII_TX_EN [LAN8742A-CZ-TR_TXEN]
PG11.Signal=ETH_TX_EN
PG13.GPIO_Label=RMII_TXD0 [LAN8742A-CZ-TR_TXD0]
PG13.Signal=ETH_TXD0
PG14.GPIO_Label=D1_TX
PG14.Signal=USART6_TX
PG6.GPIO_Label=USB_PowerSwitchOn [STMPS2151STR_EN]
PG6.Signal=GPIO_Output
PG7.GPIO_Label=USB_OverCurrent [STMPS2151STR_FAULT]
PG7.Signal=GPIO_Input
PG9.GPIO_Label=D0_RX
PG9.Signal=USART6_RX
PH0/OSC_IN.GPIO_Label=MCO [STM32F103CBT6_PA8]
PH0/OSC_IN.Signal=RCC_OSC_IN
PH1/OSC_OUT.Signal=RCC_OSC_OUT

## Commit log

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2020-01-04 Fixed a bug in Cylinder class. Got a basic Romi Motor model done.
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2020-01-08 Serious refactoring of the code to add DXF class. Also, changed object constructors to take ScadProgram argument.
    [romi_base.csv]
2020-01-09 Finished reworking the code to use the DXF classes to extract locations from .dxf files.
    [romi_base.csv]
2020-01-10 Redid PinReceptical and made it general. Also, it is possible to fetch the PCB holes from the class for 'drilling' into a PCB.
    [romi_base.csv]
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2020-02-09 Updated the README.md to show the assembly order.
    [romi_base.csv, rpi_MECH_3bplus.dxf, rpi_MECH_4b_4p0.dxf]
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2020-03-15 Added STLink, fixed some bugs with the Nucleo144 connector positions, and added PCB connectors to the Ras/Other Pi.
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2020-03-25 Fix Kicad typo on README
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2020-04-02 Fixing install_start.sh to switch over to master branch and update repository if possible.
2020-04-05 Fixed where new-lines kept getting added to end of master_board.kicad_pcb .
    [master_board.kicad_pcb]
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2020-04-23 Did intial Makefile to convert f767zi.* and kiparts/*.kipart.csv into master_board.lib .
    [f767zi.csv, hcsr04.kipart.csv]
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2020-04-25 Got kidocgen written (stored in kicube32 repo) and integrated.
    [hcsr04.kipart.csv]
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2020-04-27 Updated nucleo_144.sch to use the correct symbol for the F767ZI;NUCLEO144 .
    [nucleo_144.sch]
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2020-05-09 Broke the master PCB into a center/ne/nw/se/sw PCB's.
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2020-05-25 Fixed Kicad Footprint.hole() to do oval pads correctly.
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2020-05-31 Sonars seem to be free of mechanical interference now.
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2020-06-02 Still tracking down the missing holes problem; frankly it is an architecture error.
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2020-06-06 Reorganize footprints schematics symbols files to orders directory.
    [encoder.kicad_pcb, encoder.kipart.csv, encoder.sch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]
2020-06-06 Added encoder schematic sysbol to encoder (rev. A) schematic.
    [encoder.kipart.csv, encoder.sch]
2020-06-08 Got first footprint installed in encoder.kicad_pcb. PCBChunks are starting to work.
    [encoder.kipart.csv]
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2020-06-10 Fixed up right angle pin header artwork. Added pin 1 marker.
2020-06-10 Wrapped up encoder/rev_a it should be ready for schematic capture and wiring.
    [encoder.kicad_pcb, encoder.sch]
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2020-06-13 Created the master, center, ne, nw, se, sw Kicad Projects.
    [center.kicad_pcb, center.sch, master.kicad_pcb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]
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2020-06-14 Generate Sonar footprints; added a bunch of untracked files that should be tracked.
    [encoder_mate.kipart.csv, ne.sch, table.csv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]
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2020-06-18 Updated some of the schematics and PCB's via hr2_models.py .
    [center.kicad_pcb, center.sch, f767zi.kipart.csv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]
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2020-06-21 Temporary manual version of ne.kicad_pcb for debugging purposes.
    [ne.kicad_pcb]
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2020-06-22 Successfully placed a font surface non-rotated footprint in ne.kicad_pcb.
    [center.kicad_pcb, encoder.kicad_pcb, master.kicad_pcb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]
2020-06-22 Manually put CN60 on the back surface; need to get softare capable of doing the same.
    [ne.kicad_pcb]
2020-06-27 Revert ne.kicad_pcb to front with no rotation.
    [ne.kicad_pcb]
2020-07-11 Finally sonars placed. Had to manually specify the rotattions thought.
    [center.kicad_pcb, ne.kicad_pcb, nw.kicad_pcb]
2020-07-12 Fixed the center PCB to be generated by PCBChunks.
2020-07-12 Moved nylon tie down holes for high profile sonars.
    [ne.kicad_pcb, nw.kicad_pcb]
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2020-07-13 Got Encoder PCB's installed on the center PCB.
    [center.kicad_pcb, center.sch, encoder.kipart.csv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]
2020-07-14 Added Raspbery Pi F2x20 Connector to schematic library.
    [center.sch, raspi_f2x20.kipart.csv]
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2020-07-19 Got the ST Link and Adaptor converted over to CBChunk.
    [master.kicad_pcb]
2020-07-20 Added .../st_adaptor/rev_a directory. ST_MATE is properly integrated as a symbol/footprint.
    [ST_Adapter.kipart.csv, ST_MATE.kipart.csv, center.kicad_pcb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]
2020-07-20 ST Mate is automatically placed on the center.kicad_pcb.
    [center.kicad_pcb]
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2020-07-31 Removed old PCB class that was replaced by PCBChunk.
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2020-08-09 Added spacer mounting holes to schematics and associated PCB's.
    [M2.0.kipart.csv, M2.5.kipart.csv, M3.0.kipart.csv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]
2020-08-09 Placed all of the Groves on the PCB's.
    [GROVE20x20.kipart.csv, GROVE20x20L.kipart.csv, GROVE20x20R.kipart.csv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]
2020-08-09 Fixed Groves and added MikroBus's.
    [MIKROBUS_MEDIUM_MATE.kiparts.csv, MIKROBUS_SMALL_MATE.kiparts.csv, center.kicad_pcb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]
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2020-08-12 Got the NUCLEO placed. Readjusted a few other parts.
    [NUCLEO_F767ZI_2xF2x35.kipart.csv, center.kicad_pcb, center.sch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]
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2020-08-16 Got Bridge connectors installed on PCB's. Tweaking still required.
    [BRIDGE_NE_INNER.kipart.csv, BRIDGE_NE_OUTER.kipart.csv, BRIDGE_NW_INNER.kipart.csv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]
2020-08-16 Started working on zones. (Added zone to sw.pro)
    [sw.kicad_pcb, sw.sch]
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2020-08-17 The four corner boards ne/nw/se/sw are now zoned.
    [ne.kicad_pcb, ne.sch, nw.kicad_pcb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]
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2020-08-19 Fixed the zone fill stripping code.
    [ne.kicad_pcb, nw.kicad_pcb, se.kicad_pcb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]
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2020-08-21 Positioned all of the parts on SW board.
    [se.kicad_pcb, se.sch]
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2020-08-23 Found and fixed nasty bug in Square class.
    [encoder.kicad_pcb]
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2020-08-30 Started working on center board PCB. Clean up stale schematics.
    [U3V70xMATE_F1x4+F1x5.kipart.csv, center.sch, h_bridges.sch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]
2020-08-31 Mostly wrapped up power supply and motor driver schematics.
    [AH1806_SC59.kipart.csv, AP2114HA-3.3TRG1_1A_SOT223.kipart.csv, DRV8833PWPR_16HTSSOP.kipart.csv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]
2020-09-04 Wrapped up the first pass through Single Board Computer (i.e. Ras Pi)
    [CAT24C32.kipart.csv, MCP7940_SOIC8.kiparts.csv, U3V70xMATE_F1x4+F1x5.kipart.csv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]
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2020-09-07 Added level shifting to Sonars. Added shift register for LED's.
    [CD4504B_16TTSOP.kipart.csv, SN74HCS565Q1.kipart.csv, center.sch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]
2020-09-07 Fixed up the design rule checks for the Power supply.
    [POWER_PFET_GSD.kipart.csv, USB_B_MINI_POWER_SLAVE.kipart.csv, power.sch]
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2020-09-13 More work on README's and pin binding.
    [stm32f767_af.csv]
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2020-09-21 More pin binding.
2020-09-21 Updated signal_bindings table in pinsbind.py to allow shorts.
    [pinsbind.py]
2020-09-22 Got pin shorting to work in pinsbind.py.
    [pinsbind.py]
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2020-09-28 Finished initial pin binding of HR2 robot. Yeah!
    [NUCLEO_F767ZI_2xF2x35.kipart.csv, master.csv]
2020-09-28 Fixed some comments in pinsbind.py
    [pinsbind.py]
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2020-10-04 Reworked Sonars, Servers, and LED's schematics.
    [LM66100_SOT363.kiparts.csv, NUCLEO_F767ZI_2xF2x35.kipart.csv, SERVO_F1x3.kipart.csv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]
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2020-10-25 Fixed corruption of order1.lib file.
    [GROVE20x20.kipart.csv, GROVE20x20L.kipart.csv, GROVE20x20R.kipart.csv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]
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2020-10-28 Flipped Grove and Mikrobus connectors to the back side.
    [master_board.kicad_pcb, wowbus.sch]
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2020-11-15 Fixed board cuts contours.
    [master_board.kicad_pcb]
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2020-11-24 Fixed SPI shift registers (good find by James Nugen\!)
    [connectors.sch, leds.sch, master_board.kicad_pcb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]
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2020-12-05 Change to sch and pcb
    Made following changes:
    - Remove Mikrobus connectors from sch and pcb
    - Change board to 4 layers
    - Add GND layer
    - Add 5V layer
    - Add 3.3V zone to 5V layer (experiment)
    [connectors.sch, master_board.kicad_pcb, master_board.sch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]
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2020-12-06 Change to 5V layer
    - Change PWR layer back to 5V
    - Add grid lines around and through header connectors
    - Add traces to all 5V connections on 5V layer
    - Fix DRC error about unclosed polygon on edge layer
    (Caused by duplicate edges on board outline and inner holes)
    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
    [master_board.kicad_pcb]
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2020-12-06 Fixed the schematic DRC errors.
    [connectors.sch, master_board.sch, nucleo144.sch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]
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2020-12-09 Changed bypass caps and sonar echo outputs
    - Changed bypass caps to 0.1uF
    - Removed voltage dividers on sonar echo outputs to Nucleo
    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
    [connectors.sch, leds.sch, master_board.kicad_pcb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]
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2020-12-14 Changes to encoder and st_adapter
    Changed AH1806 symbol in encoder.sch
    Changed resistor sizes in encoder sch and pcb
    Kicad migrated st_adapter sch to new format
    Added part designations to st_adapter pcb
    [encoder.kicad_pcb, encoder.sch, st_adapter.kicad_pcb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]
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2020-12-17 Added missing BOM.csv files.
    [encoder_kicad_bom.csv, master_board_kicad_bom.csv]
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2020-12-21 Fixing DRC errors.
    [master_board.kicad_pcb]
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2020-12-24 Fixed SN74C596 schematic symbol.
    [SN74HC166_TTSOP16.kipart.csv, SN74HC595_HTSSOP16.kipart.csv, SN74HCS565Q1.kipart.csv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]
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2020-12-25 Missed a couple of schematic sheets.
    [leds.sch, master_board.sch]
2020-12-25 Corrected Optorelay current resistors.
    [master_board.kicad_pcb, master_board_jlcpcb_bom.csv, master_board_kicad_bom.csv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]
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2020-12-25 Fixed I2C pull-ups on RasPi.
    [master_board.kicad_pcb, master_board_jlcpcb_bom.csv, master_board_kicad_bom.csv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]
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2020-12-29 Added some missing files.
    [encoder_jlcpcb_bom.csv, master_board_jlcpcb_bom.csv, master_board_kicad_bom.csv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]
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2021-01-30 No longer updated board outlines of encoder, master_board, and st_adapter.
    [spacers_standoffs_#2.csv]
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

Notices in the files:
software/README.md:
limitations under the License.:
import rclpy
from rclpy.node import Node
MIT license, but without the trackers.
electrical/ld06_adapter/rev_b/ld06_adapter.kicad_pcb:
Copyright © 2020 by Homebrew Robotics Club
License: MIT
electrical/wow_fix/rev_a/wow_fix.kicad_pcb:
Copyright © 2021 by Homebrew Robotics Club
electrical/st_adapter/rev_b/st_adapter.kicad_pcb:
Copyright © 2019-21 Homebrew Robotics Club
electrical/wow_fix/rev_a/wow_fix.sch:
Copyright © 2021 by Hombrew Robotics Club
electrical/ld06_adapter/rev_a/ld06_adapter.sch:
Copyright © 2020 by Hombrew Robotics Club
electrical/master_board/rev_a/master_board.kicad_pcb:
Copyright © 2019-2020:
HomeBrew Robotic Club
